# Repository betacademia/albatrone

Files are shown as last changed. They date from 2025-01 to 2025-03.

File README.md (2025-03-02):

# Albatrone

For the biomimicry minor of the Makerspace, localised at the University of Amsterdam, team Albatrone has done some design and research. The final part of the paper, documentation, will mostly refer to this repository, since it will contain all the (final) digital work done for the minor.

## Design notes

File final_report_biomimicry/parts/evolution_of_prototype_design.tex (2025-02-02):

\sectionauthor[Simon Blom; Romy Schardam]{Evolution of Prototype Design}
% This chapter is where you document the entire journey of your prototype's development. It should not only showcase your final product but also the thoughtful and iterative process that led to its creation. This narrative should be detailed and reflective, offering a comprehensive and transparent view of your design process. This chapter is your opportunity to demonstrate your team's problem-solving skills, adaptability, and ability to integrate feedback into a practical solution.
% \begin{itemize}
%     \item Step-by-Step Evolution: Describe each stage of your prototype's development. This should include the initial concept, any interim versions, and the final design. For each step, explain the rationale behind the design choices made, focusing on both the successes and challenges you encountered.
%     \item Design Motivation: Detail the motivations for each design change. These motivations can be varied - they might stem from your own insights, experimentation, feedback from stakeholders, or new information from scientific literature. It's important to articulate why each change was made and how it contributes to the overall effectiveness of your prototype.
%     \item Stakeholder Input: Discuss the stakeholders involved in your project, providing insights into their perspectives and how their feedback has influenced your approach. For each stakeholder, include a concise summary of the interview. These summaries should be approximately half a page each and should detail the stakeholder's role, their perspective on the problem you are addressing, and any specific insights or recommendations they provided. Clearly indicate which team member conducted each interview.
%     \item Influence of Stakeholder Insights: Specifically address how stakeholder input influenced your design evolution. Explain how their insights led to adjustments in your design, alterations in your theoretical approach, or shifts in your understanding of the societal impact of your solution. This aspect should clearly link the feedback you received to tangible changes in your prototype.
% \end{itemize}

\section{The beginning of the project} 
At first, the idea was to make a drone that could take other drones out of the air by flying into them. This idea was quickly shut down as it became clear that this would involve a lot of precision when calculating the flight trajectory of the other drone, making sure our drone was fast enough to catch up, and making sure it could change its trajectory really fast when needed.

The brainstorming continued and eventually led to the idea of the Albatrone. A fixed wing drone with the aim to increase the airtime of the drone which could be used for search and rescue applications.  

\subsection{Problem statement}
The aim of the Albatrone is to solve the problem of the limited airtime of drones. Drones like a quadcopter need constant energy to keep flying. This leads to the need for a large, and most likely heavy, power supply when the drone needs to be in the air for a longer amount of time. Thereby adding to the energy needed to keep the drone in the air. The goal is to make a drone that is able to take advantage of its environment. With the fixed-wing design, the Albatrone will be able to glide through the air, eliminating the need for a constant power supply. 

\subsection{Midterm proposal}
\subsubsection{Background information and research}

In the beginning, the choice was made to take inspiration from the albatross. This decision was made on the basis of a quick google search on the top birds that use gliding to save energy during long flights. Adding to the fact that the wandering albatross has the biggest wingspan out of all birds and that the albatross is a heavy bird, this decision was quickly accepted by all members of the team.  

To solidify this decision even further, research was done on the different properties, like the lift coefficient, drag coefficient, and the relation of both coefficients to the angle of attack, of a few foils (cross sections of the wing) that were based on different animals. For this XFoil was used. XFoil is a software developed at the Massachusetts Institute of Technology. XFoil is an interactive program for the design and analysis of subsonic isolated airfoils (\cite{XFoil}). Within the database, there are three different albatross foils
\begin{itemize}
    \item GOE 176 (ALBATROS 7020) AIRFOIL (goe176-il) (\cite{Foil_176}) - one dragonfly foil (\cite{Flcn})
    \item GOE 174 (ALBATROS 5020) AIRFOIL (goe174-il) (\cite{Foil_174}) - a falcon foil (\cite{Drfly})
    \item GOE 173 (ALBATROS 6020) AIRFOIL (goe173-il) (\cite{Foil_173}) - a wasp foil (\cite{Wasp})
\end{itemize}
and when comparing all these foils, the dragonfly foil came out on top.

Another conformation is found in the paper called ‘Aerodynamic characterization of an Albatross wing for Bio-inspired unmanned aerial vehicle’ (\cite{Bio_unmanned}). In this paper, the researchers found that the albatross wing has a higher lift coefficient, and a lower drag coefficient compared to the wing shapes of the other birds.

The way in which the albatross can traverse long distances without needing a break is also due to the way in which the albatross harnesses the energy from its environment.

One interesting aerodynamic interaction of the wings is created by the Bell-Shaped Lift Distribution (\cite{Evolution_Alba}).

Lift is generated by vortices. In the Bell-Shaped Lift Distribution, the vortices are shed at around 70-80\% of the span. This explains why the wingtips of the albatross are not going up even when they undergo speeds around 3G during dynamic soaring. The benefit of a Bell Shaped Lift Distribution is that it generates a local induced thrust. Although the net force still results in net drag, this local thrust is interesting (\cite{Evolution_Alba}). 

The albatross uses two types of soaring: dynamic soaring and thermal soaring.\\

In dynamic soaring, the albatross makes use of the varying wind speeds above the sea surface. Dynamic soaring consists of four stages, the climb into the wind (wind ward climb), the turn at high altitude, the leeward descent, and the low-altitude turn (see Figure \ref{fig:Dynamic soaring}). During this cycle, the albatross has a decrease in energy when it is close to the water, but an increase when it climbs the wind. Because the albatross gains its energy back, it takes almost no energy to keep it in the air (\cite{Evolution_Alba}). 

\begin{figure}
    \centering
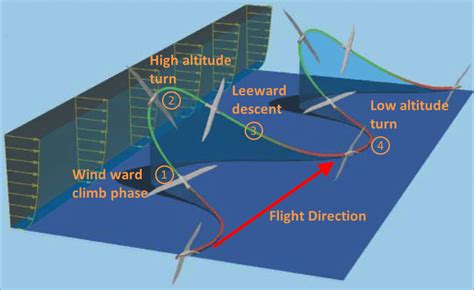
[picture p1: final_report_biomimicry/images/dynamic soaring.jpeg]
    
    \caption{Dynamic soaring cycle (\textit{https://www.researchgate.net/figure/Dynamic-soaring-cycle_fig1_326672558})}
    \label{fig:Dynamic soaring}
\end{figure}

Next is thermal soaring. During thermal soaring, the albatross flies through or circle in columns of warm air currents that rise from the ground. The rate of descending of the bird is less than the magnitude of the rising air. This makes it possible for the birds to attain more altitude, see Figure (\ref{fig: thermal soaring}). With this extra altitude, the albatross is able to glide to the next thermal (\cite{Evolution_Alba}). 

\begin{figure}
    \centering
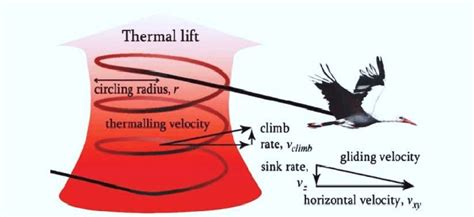
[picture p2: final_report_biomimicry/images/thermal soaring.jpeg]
    
    \caption{Thermal soaring (\textit{https://www.researchgate.net/figure/Thermal-Soaring-16_fig4_352395064})}
    \label{fig: thermal soaring}
\end{figure}\\

This paper also mentions that even the colors of the wings can have some effect on the endurance of the bird. The temperature difference between the upper (black) and the lower (white) surface of the wings, aids in drag reduction. Temperature plays a significant role in the reduction of induced and skin friction drag.\\

Researchers found that the black-white or black-black wings performed better than the white-black or white-white coloring (\cite{Evolution_Alba}).\\

\subsubsection{What does the Albatrone take from the albatross?} 

Mostly, the shape and the dimensions of the wings. To make the wing structurally sound, the bones in the albatross wing will be taken as inspiration. This is done by having 3D printed joints and the ‘bones’ make out of pieces of balsa wood. The idea is to follow the shape of the wing as best as possible, also making sure the cross section is the same. \\

If possible, the tail feathers of the albatross could also serve as an inspiration for the horizontal stabilizers. For this to work, the placement of the propeller needed to be taken into account.
As told by the expert stakeholder ir. Madeline Zhang, the placement of the propeller has an impact on the stability of the drone. She mentioned that placing the propeller on the back of the drone makes it more stable as it does not cause the airflow over the wings to become turbulent. Placing the propeller in front, means an added risk of the drone back-flipping on take-off. If the propeller is mounted at the back of the Albatrone, the stabilizers should not obstruct the propeller.
 
\begin{figure}
     \centering
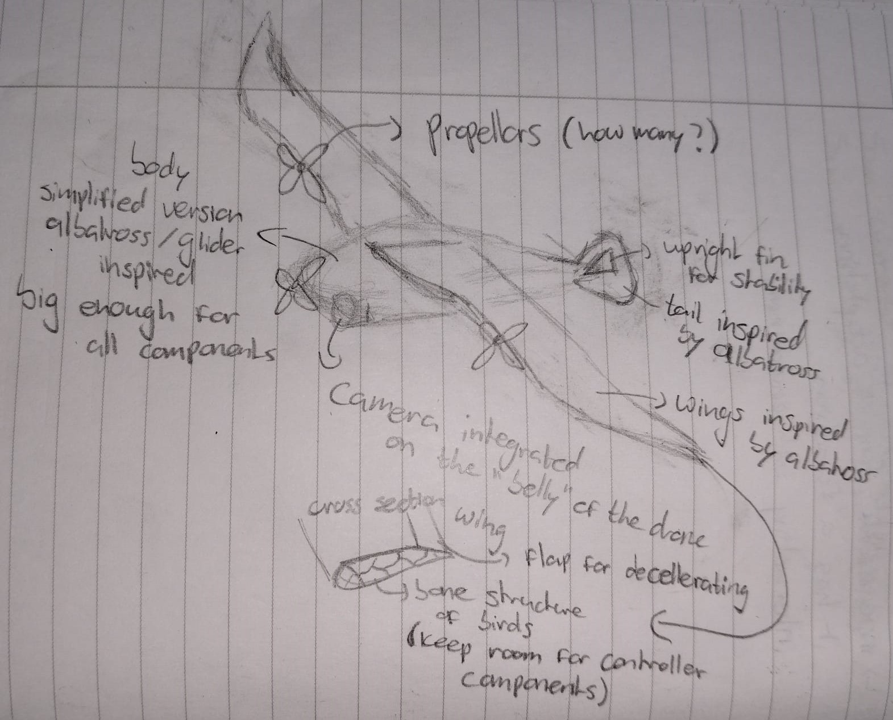
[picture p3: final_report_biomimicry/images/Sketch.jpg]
     
     \caption{One of the first sketches of the Albatrone}
     \label{fig:Sketch Albatrone}
 \end{figure}

 In figure \ref{fig:Sketch Albatrone}, one of the first sketches of the Albatrone can be seen. Highlighted are the wings, tail, body and bone structure that are inspired by the albatross. \\

\section{Design evolution} 

During the time between the project proposal and the final report, some changes occurred. 

\subsection{Material} 
In the beginning of this design process, our 'plan A' was to use a Carbonfiber-nylon filament (PAHT-CF). During a meeting with our expert stakeholder Ir. Madeline Zhang, she mentioned that making the Albatrone out of balsa wood and shrink foil would be a good option to keep it lightweight. While making the Albatrone out of wood was an option, the availability and prices online, plus the lack of modes of transportation to get the wood to the Makerspace, made this option not final. The people of the Technology Center also provided feedback during a project standup session. Here they mentioned that balsa wood and shrink foil might not be strong enough to hold the electronics. This lead to researching ways to improve the structural stability. I-beams were an option, but most I-beams are made of metals. A wooden I-beam was really expensive and not made of the lighter balsa wood.

Another option that was presented by the project staff was styrofoam. This option was briefly explored. However, the shaping needed to be done with a foam cutter. This required a steady hand from the cutter and the shape of both wings needed to be the same. Having two identical but mirrored versions of an albatross wing out of styrofoam, seemed unlikely.

With a little more research, a different filament, Bambu PLA Aero, was found to be suitable for the Albatrone. This filament is a sort of "active foaming PLA" specially advertised by use for Remote Controlled Planes (\cite{PLA_Aero}). This change did mean that some different dimensions were needed as every part needed to fit in the BambuLab X1 Carbon or X1E. This also meant that 3D printed 'joints' and wooden 'bones' were no longer needed. While losing this bio-mimicry component, it now became possible to incorporate the hollow bone structure of birds by the configurable sparse infill of those 3D printers. Again, the people from the Technology Center provided feedback. They were a little hesitant at first and mentioned that most plastics had a similar density and could be too heavy for our application. On the other hand, when the properties of the PLA Aero were explained, they became intrigued. This solidified our choice in material.

When ordering the filament, Murphy's law struck again. On the website of `Electronica voor jou', it said that there was one roll of black PLA Aero available. The filament was ordered on the 10th of December, after contacting the business three separate times and waiting for over a month (13th of January), they finally said they could not order this specific PLA. The PLA Aero was ordered by a different business, only this time in white. As mentioned in the 'Background information and research' part, black-white or black-black wings create (even if it is just a little) less drag compared to the white-black or white-white wings. While this color change will most likely not be responsible for big changes in the performance of the Albatrone, especially during winter, it could be interesting to try and recreate these findings on the Albatrone in the future. While waiting for the right filament to arrive, parts of the design was printed using regular PLA. These prints were used to test the way the parts are attached to each other and the tolerances of the BambuLab printers.

\subsection{Wing dimensions} 
Another change, the dimensions of the wings. The biggest chord length was estimated to be around 270 mm for the smaller gray-headed albatross. This was based on an estimation that the wing is roughly 1/3 of the length of the body of the albatross. This estimation came from measuring a picture of the gray-headed albatross from google. 

The length of the body of was found to be in the range of 71 to 82 cm (710 to 820 mm) (\cite{WoRMS}).

To get the top view of the wing, the length of the bones (humerus, ulna, and the manus + primaries) were used to get an idea of how long each part must be (\cite{Wing_shape}). The wingtip is put at a 60 degree angle to make it easier to calculate the area of the wing. 

In the same paper, the aspect ratio of the gray-headed albatross (or the Diomedea chrysostoma), is found to be 15.3. with a wingspan of 200 cm.  

To find the aspect ratio, the wingspan squared is divided by the wing area.\\

To get to an aspect ratio close to this 15.3, the chord length needed to be smaller than expected.\\

Calculating the aspect ratio should be somewhat simple. Unfortunately, it would not be a (school) project without even the smallest things going wrong. A while after using the aspect ratio as a guide on how big the chord length of the different parts of the wing should be and keeping in mind that during this calculation the dimensions of the body was just an estimate, the realization that in all those calculations the area of the body was wrongly calculated came a little too late.\\

As mentioned above, the chord length started at 270 mm. Limited by the dimensions of the 3D printer, this became 250 mm. After realizing the mistake in the calculation of the aspect ratio, the only 'quick fix' that came to mind was to make the first part of the wing shorter both in length and width as the thickness needed to intergrade the servo that controls the ailerons in the middle part of the wing, was set to 145 mm. The maximum chord length ended up being 150 mm which quickly goes to 145 mm for most of the wing.\\

\subsection{Body} 
The journey to the perfect body. In the beginning, the idea was to make the body a more simplified version of that of the albatross. This meant following the general shape of the albatross without the beak. However, designing organic shapes in SolidWorks or Fusion was proven to be tricky as is evident by the first attempt of the wing design in Figure \ref{fig:Fusion wing fail}.\\

\begin{figure}
    \centering
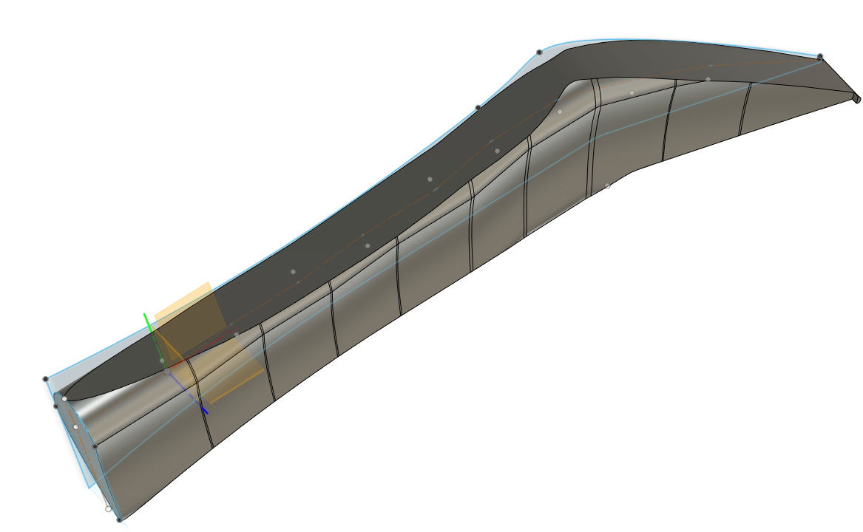
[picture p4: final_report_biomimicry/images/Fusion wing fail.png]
    
    \caption{First attempt designing the wing in Fusion}
    \label{fig:Fusion wing fail}
\end{figure}\\

To keep the design manageable, the body ended up more cylindrical as can be seen in Figure \ref{fig:Cylindrical body}, but not without trying the other things that came to mind.\\

The first few iterations mostly resembled a bullet shell, see Figure \ref{fig:bullet shell} and \ref{fig:Unfinished bullet}. In the second figure, the idea was to make the walls straight to make it easier for the wings to attach to the body. Figure \ref{fig:Eehm...no} was an attempt to make a symmetrical body with straight walls for the wing attachment. This did not really work. So, a little more thinking was needed before going to SolidWorks.
The resemblance to a bullet occurred most likely because the head and body were attached together. Again, because the limitations of the available printing dimensions, this was not the right approach. \\

To get the desired length of the whole body, the body, head and tail were separated. To make sure the inside of the body could be reached, a part of the body was cut horizontally. Next slots were added to be able to attach the rest of the body to this open part. The head, tail and wings would hopefully keep the body closed during flight. Figure \ref{fig:Cylindrical body} and \ref{fig:Oval top} were designed more carefully.

\begin{figure}
    \centering
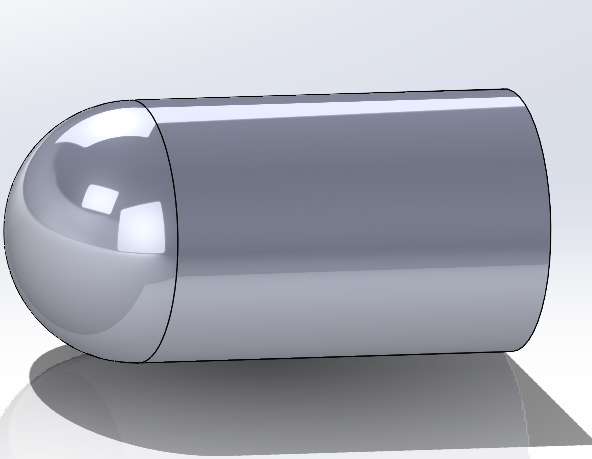
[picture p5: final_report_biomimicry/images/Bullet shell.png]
    
    \caption{Bullet shell body}
    \label{fig:bullet shell}
\end{figure}

\begin{figure}
    \centering
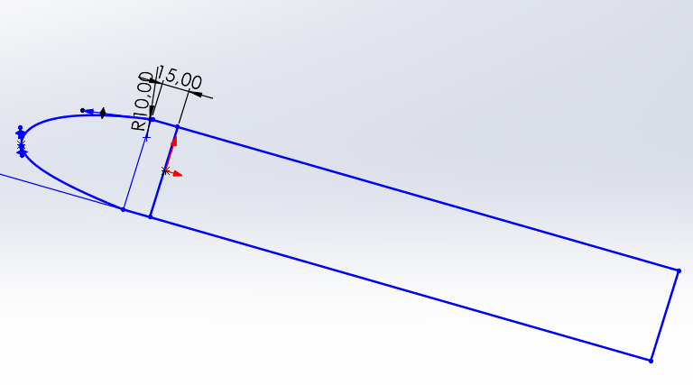
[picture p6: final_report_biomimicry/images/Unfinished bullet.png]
    
    \caption{Sketch straight-walled bullet body}
    \label{fig:Unfinished bullet}
\end{figure}

\begin{figure}
    \centering
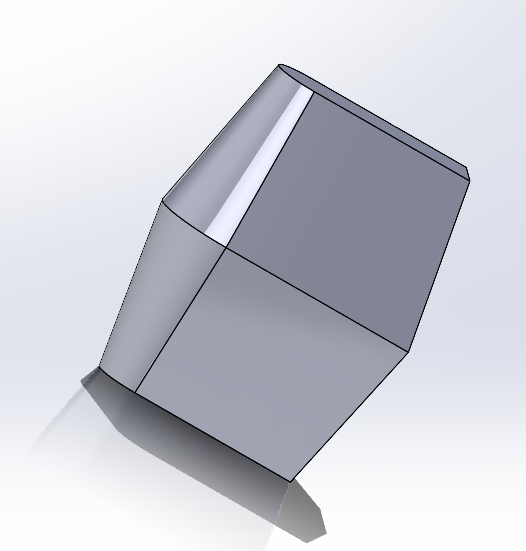
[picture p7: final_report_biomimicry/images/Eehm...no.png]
    
    \caption{Attempt to make a symmetric, straight-walled body}
    \label{fig:Eehm...no}
\end{figure}

\begin{figure}
    \centering
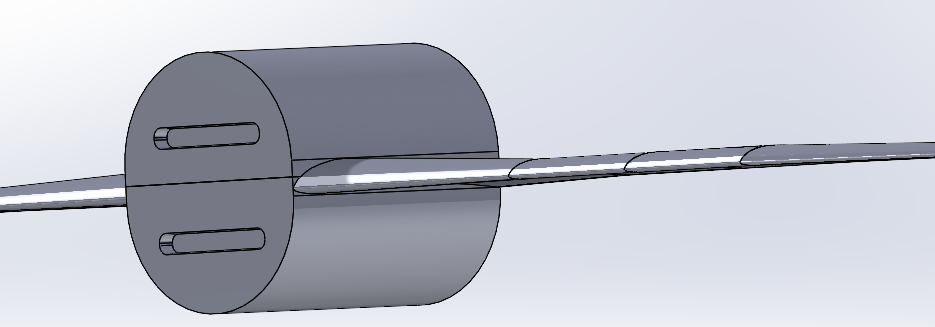
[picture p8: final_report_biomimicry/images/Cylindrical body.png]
    
    \caption{Cylindrical body}
    \label{fig:Cylindrical body}
\end{figure}

\begin{figure}
    \centering
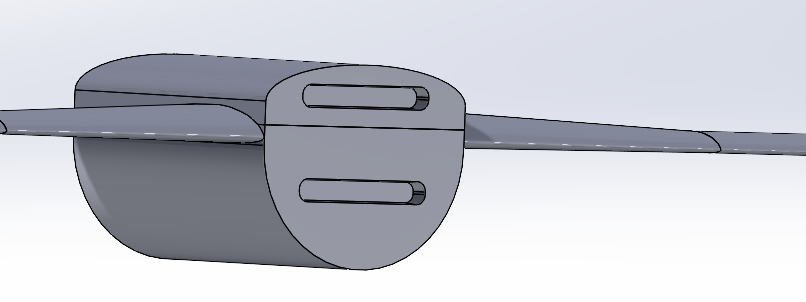
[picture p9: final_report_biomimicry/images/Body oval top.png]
    
    \caption{Body with oval top}
    \label{fig:Oval top}
\end{figure}

Not only the shape of the body went through some iterations, but also the dimensions. The planned width of the body was around 200 mm to get the wingspan close to the 2 meters from the gray-headed albatross. In the end, this changed. The choice was made to design the body as small as possible, while still being able to hold all the electronics. This decision was based on the insight that the body would most likely only negatively affect the aerodynamics as the bulk of the body would be a cylinder. The design in Figure \ref{fig:Cylindrical body} was first made with a radius of 55 mm on the outside with a wall thickness of 2 mm. This made the whole body quite big in relation to the cross-section of the wings. To save on material, weight and hopefully improve on the aerodynamics, the top was designed to be more oval. This change did not go as smoothly as thought. SolidWorks began moving points when changing the height of the ellipse in the sketch or did not connect the sketch of the ellipse to the right point in the sketch. This made it quite difficult to accurately design the body. After deleting, redrawing, and double checking the sketches again and again, the body did eventually line up. However, in the mean time, the electronic parts had arrived. This meant that is was now possible to design the body more around the electronics. This took away the some of the guesswork with regards to the size needed. With a smaller body, the drag would decrease and the weight would decrease, resulting in better aerodynamic properties. Keeping the issues with the oval top in mind, this smaller body design went back to the two half circles as seen in Figure \ref{fig:Cylindrical body}.

\subsection{Tail} 
The main goal for the tail is to be able to stabilize the drone with the vertical and horizontal stabilizers [https://aerotoolbox.com/design-aircraft-tail/]. The process of designing the stabilizers is explained later. For the shape of the tail of the Albatrone, inspiration was taken from pictures of the tail of planes. Looking at pictures of planes, it was noted that in a lot of pictures, the underside of the tail curves up. Keeping the top line of the plane straight. Figure \ref{fig:Tail v1} shows the first iteration of the tail. Figure \ref{fig:Albatrone small body} shows the tail more in line with the top of the body.\\

\begin{figure}
    \centering
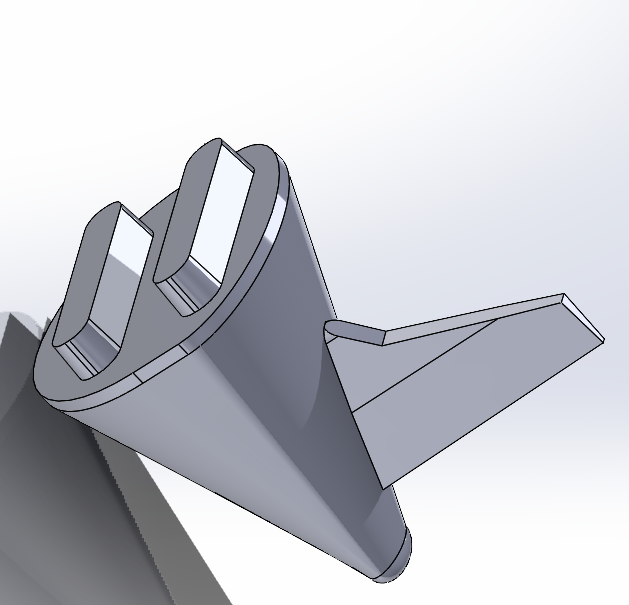
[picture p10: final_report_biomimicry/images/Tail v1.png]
    
    \caption{Tail design more centered on the body}
    \label{fig:Tail v1}
\end{figure}

\begin{figure}
    \centering
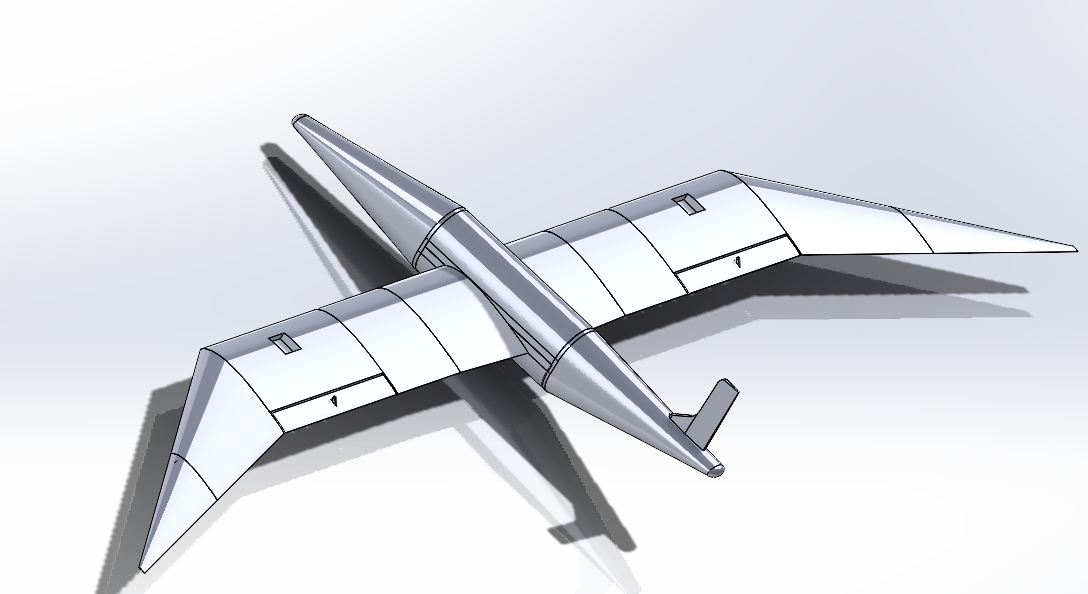
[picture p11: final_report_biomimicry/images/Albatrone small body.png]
    
    \caption{Albatrone where tail is more in line with the top of the body}
    \label{fig:Albatrone small body}
\end{figure}

\subsection{Head} 
As mentioned before, first the design for the head mostly resembled a bullet shell. When it became clear the body also needed to be printed in sections, the head of the Albatrone became more of a cone shape, similar to the tail, as can be seen in Figure \ref{fig:Albatrone small body}. However, this was mostly due to a lack of knowledge on how to create a more plane-like nosecone, With the help from a YouTube tutorial called 'Solidworks Loft Basics - Design an Aircraft Nosecone (CAD Tutorial for Beginners! - B737 \& F-22)' from VDEngineering, the nosecone became more similar to a 'normal' nosecone from a plane (\cite{Nosecone}). To follow this tutorial, a side, top, and front view was needed. This, unfortunately, meant that it was not possible to just use any picture. To still keep the spirit of using the albatross, a blueprint of the Aero L-39 Albatros was used to design the head (\cite{DrawingNC}). With the help of the tutorial, the head now looked as in Figure \ref{fig:Plane nose}. The choice of the plane was purely based on the name and which plane seemed to have a pointier nose as to mimic the beak of the albatross even if it is just a little. If time had allowed, it would be possible to create multiple noses and see which one worked better. Unfortunately, this was not possible in the time that was left for the project.\\

\begin{figure}
    \centering
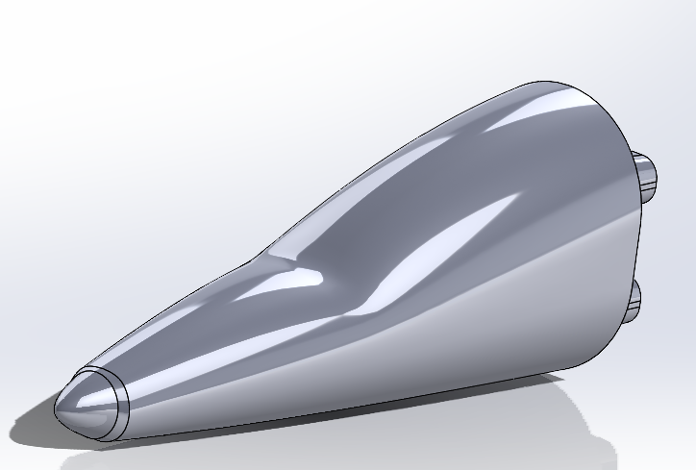
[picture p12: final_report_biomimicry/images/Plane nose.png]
    
    \caption{Head inspired by the Aero L-39 Albatros}
    \label{fig:Plane nose}
\end{figure}
\\

\subsection{Control surfaces}
To be able to control the drone, control surfaces are needed. An overview of the control surfaces of a plane can be seen in Figure \ref{Control surfaces} For the wings this meant that one middle part needed a flap to be able to manipulate the airflow around the wing (ailerons). At first, to test if it was possible, a small rectangular grove was cut out of the wing. This resulted in a totally detached flap that needed to be accurately positioned on both sides of the wing to keep symmetry. Next, the idea was to keep the upper part of the flap attached to the wing and making the cut on the bottom at an angle to make it able to go down. This would fix the problem of the positioning but decreases the mobility. Also, this idea would take some trial and error as the thickness of the connection would determine the force needed to move the flap. The higher the force needed to move the flap, the more powerful (and most likely bigger and heaver) the servo needs to be.\\

\begin{figure}
    \centering
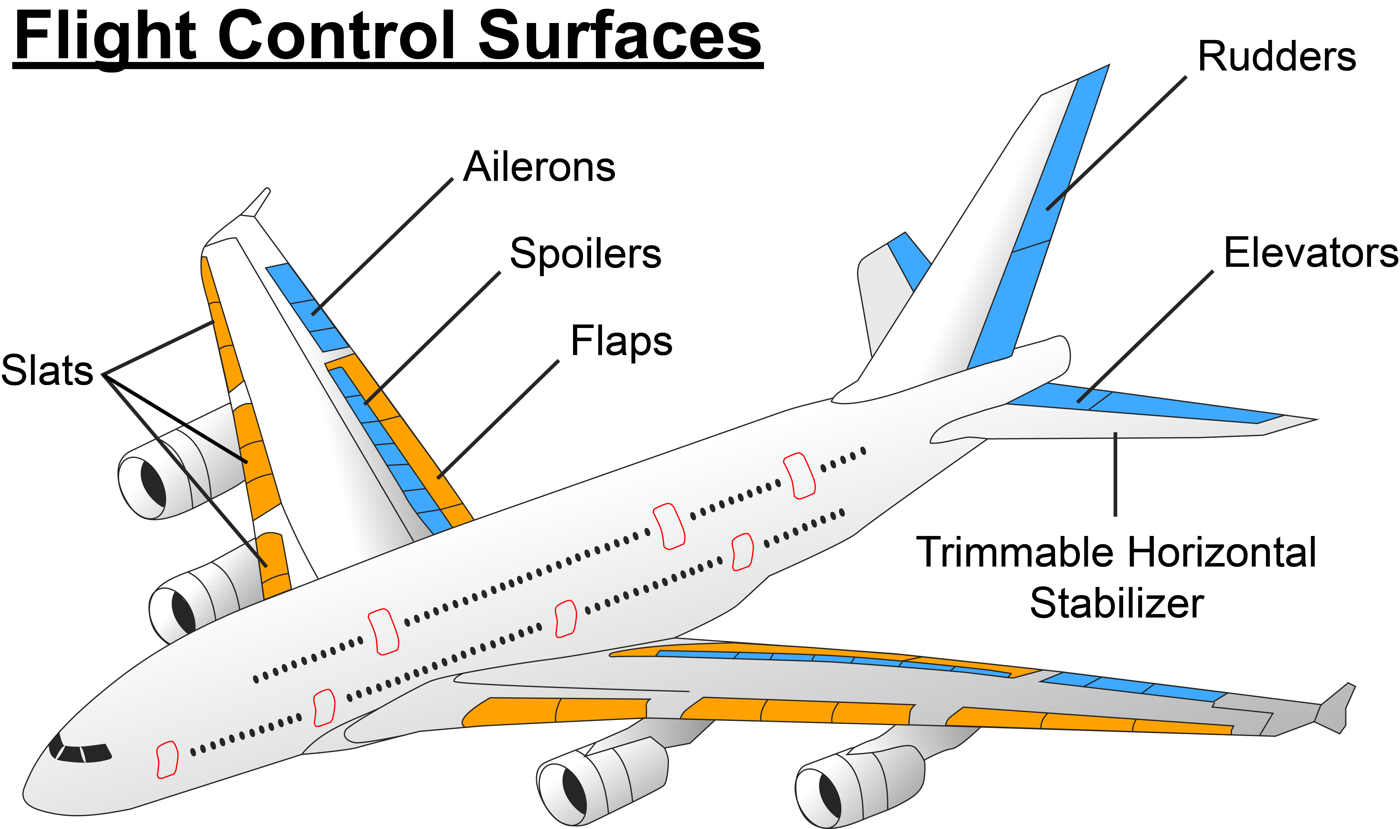
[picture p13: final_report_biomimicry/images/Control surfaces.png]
    
    \caption{Overview of the control surfaces of a plane (\textit{https://www.naii.com/DesignExamples/TestingAircraftControlSurfaces})}
    \label{Control surfaces}
\end{figure}

Eventually, the design is based on a tutorial found on youtube.com called 'Solidworks | Wing control surface animation | Aileron animation in solidworks' by Rao Aerospace (\cite{Aileron}). In this design the aileron is attached to the rest of the wing with a rod. For the Albatrone, a longer skewer should do the trick.

As for the vertical stabilizer, the first attempt was just a rectangle on the tail. After taking some inspiration from google images on tails of planes, there was an attempt to make it a little more aerodynamic. This resulted in the design in Figure \ref{fig:Sketchy vertical stab}.

\begin{figure}
    \centering
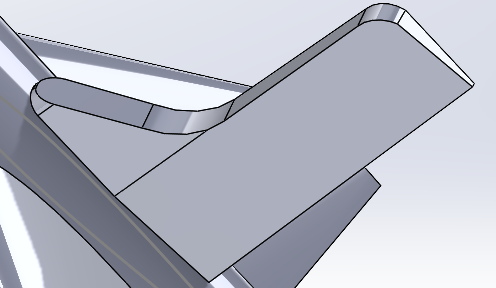
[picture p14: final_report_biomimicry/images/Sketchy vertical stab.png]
    
    \caption{Attempt at making the vertical stabilizer more aerodynamic}
    \label{fig:Sketchy vertical stab}
\end{figure}

Realizing the horizontal stabilizers are quite important as they make sure a plane is stable during a flight, more research needed to be done. First, another expert stakeholder, a neighbor of one of the members of the team (Romy) and an retired pilot that sails as a hobby, was nice enough to lend out his study books on planes, high-speed aerodynamics, and even one on the aero-hydrodynamics of sailing. While being very interesting, these books talked more about how to control a plane and not really on the design of the plane. However, during the talk with the neighbor, he advised to use the a wind tunnel to figure out what design works better and could be implemented in the design. He mentioned that calculations are nice, but some things cannot be calculated. Therefor, having access to a wind tunnel and analyzing the results, was more useful. Again, if time had allowed, adding different stabilizers to the Albatrone and noting the difference in the stability, would be ideal.

Focusing on the design of the stabilizers, a google search lead to a more useful page on Aircraft Horizontal and Vertical Tail Design (\cite{Stablizers}). This page mentions the different configurations, a relation to calculate the minimum area of the stabilizers based on some parameters from both the wing and the horizontal stabilizer itself. This page also presented an answer on the question what shape could be used for the stabilizers. A very common choice is apparently either the NACA 0010 or NACA 0012 airfoil. Comparing these airfoils again on airfoiltools.com, the NACA 0012 looks to be a little more stable than the NACA 0010, thus the decision on the airfoil for the horizontal stabilizers was made. Figure \ref{fig:Horizontal stab} shows the end result of hours full of struggling with lofts, deleting and redrawing the sketch of the curves on the sketch plane, and checking again and again if the two stabilizers are in fact symmetric and placed at the same location on the tail. At the time of writing, the elevators and the corresponding servo attachment and designated servo spot are not yet implemented.

Because this airfoil is most likely more aerodynamic than the vertical stabilizer seen in Figure \ref{fig:Sketchy vertical stab}, this airfoil will also be used as the vertical stabilizer (not yet implemented at time of writing).

\begin{figure}
    \centering
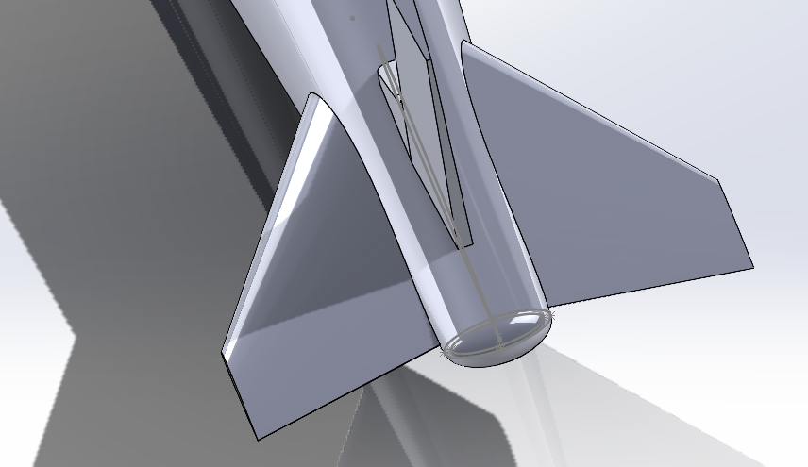
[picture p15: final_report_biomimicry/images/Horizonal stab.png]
    
    \caption{Horizontal stabilizers}
    \label{fig:Horizontal stab}
\end{figure}\\

\subsection{Connections}
It should not come as a surprise that the Albatross is made of separate parts. All those separate parts need to be connected. The connection between the different parts of the wing was quickly designed.The people of the Technology Center were not entirely sure these connections would hold up because of the stress concentrations created by such a connection. However, when testing the connections when printed with regular PLA, they proven to be strong enough to withstand the not-so-scientific stress test called 'trying our best to break them using our hands'. Another option, more in the direction of duck tails, see Figure \ref{fig:T-ducktails} was also tested. The test print looked as in Figure \ref{fig:Attachment test}. As the tolerance on these test prints was too large for our application, this idea was scrapped. 

\begin{figure}
    \centering
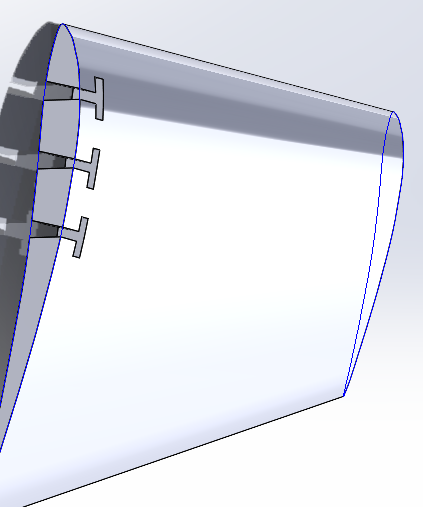
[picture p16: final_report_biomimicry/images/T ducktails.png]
    
    \caption{T-shaped duck tail inspired attachment method}
    \label{fig:T-ducktails}
\end{figure}\\

\begin{figure}
    \centering
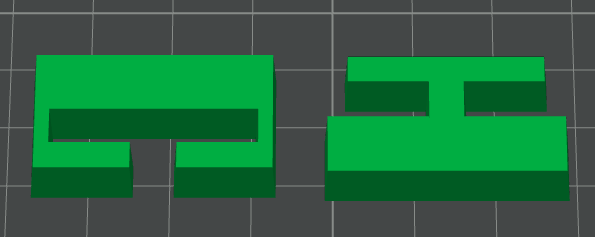
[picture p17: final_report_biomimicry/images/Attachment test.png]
    
    \caption{Test print T-shaped ducktails}
    \label{fig:Attachment test}
\end{figure}

The connection between the wing and the body required a little more thought. To test the best angle of attack for the Albatrone's wings, this attachment needed to allow one degree of freedom, the rotation. To allow for this rotation, a pin and hole connection was implemented; see Figure \ref{fig:Body pin connection}. Also visible in this figure are the connections between the other parts of the body (see \ref{fig:Tail v1} for the other part of the connection)

\begin{figure}
    \centering
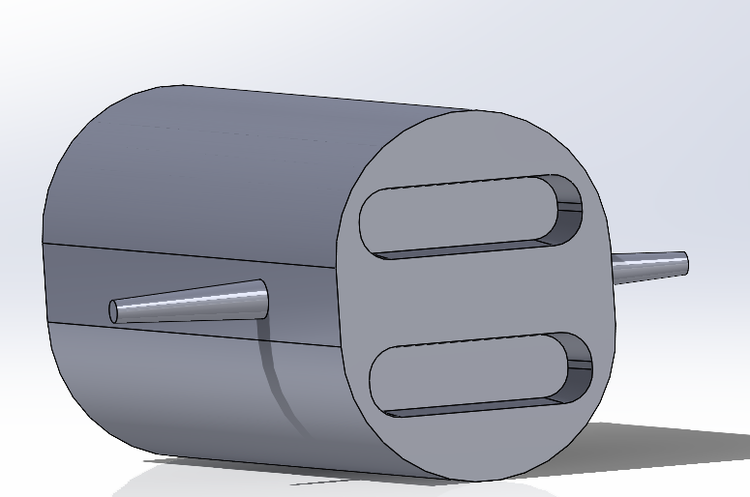
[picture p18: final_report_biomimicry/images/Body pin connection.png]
    
    \caption{Body with pin to connect to the wing}
    \label{fig:Body pin connection}
\end{figure}

As described above, this middle part of the body is cut in two to make it easy accessible. These two parts are held together by the pin-hole connections between the body and the wing and also by the extrusion and hole slots in the extra body parts made in order to get the desired length.\\

\subsubsection{Final design}
After implementing aforementioned design choices, the current final design can be seen in Figure \ref{fig:Final design}. The horizontal and vertical stabilizers are not finished yet. The horizontal stabilizers need elevators and room for the servo. The vertical stabilizer will be changed to the NACA 0012 airfoil. At the time of writing, the printing of the Albatrone is not done and is therefor also not tested. If in the next few days changes need to be made, this will obviously not be recorded in this specific report.

\begin{figure}
    \centering
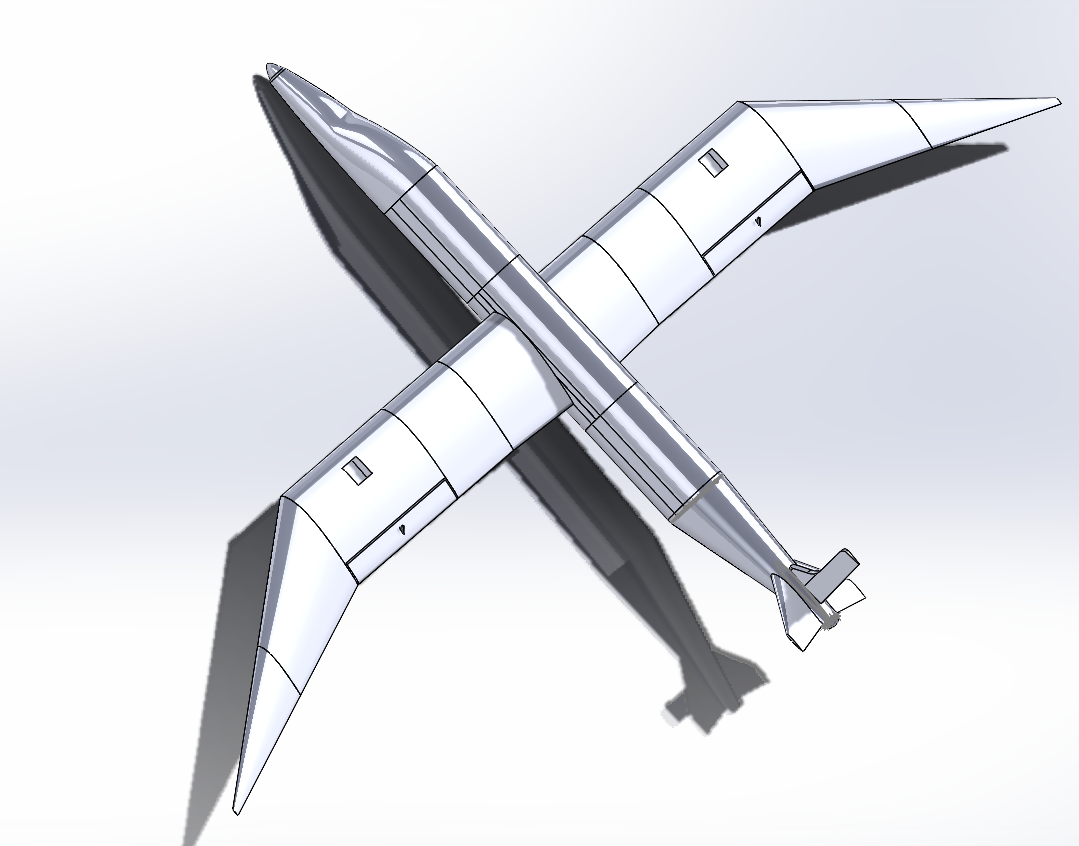
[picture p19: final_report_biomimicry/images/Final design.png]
    
    \caption{Final design}
    \label{fig:Final design}
\end{figure}

\subsection{Stakeholders}
As briefly touched upon in the text above, some design changes were made due to feedback or insights from stakeholders.

In the morning of November the 4th, we had a meeting with a police detective and specialist on the drones unit. Before the meeting, the idea was to use a combination of Lidar and Radar to obtain information about the surrounding. He explained to us that a simple camera can be enough. The power of machine learning is so powerful, that the algorithm can help more than enough. He also redirected us to an initiative called Avy. Avy makes the drone and finishes the paper work, so that the police can buy it and use it immediately. Avy was not responsive for a long period of time, but it was managed to make an appointment in the week of the presentations.

In the afternoon of November 18th, one of the members of the team attended the opening of E.N.G.A.G.E. which is the first so-called gameroom in the Department of Defense. It was organized by the "Korps Mariniers", and there were a lot of demos at the location. One of those demos was about Unmanned Aerial Systems (UAS), by the Head Coordinator of the Marine training center. I told him about our project, and we exchanged contact information. Around 10 days later we got an email cc'd from him, asking a colleague if he knew someone to help us out. 10 more days later, he responded and we were referred to someone else. This started a chain of replies and forwards, and January 20th we ended up with a specialist from the UAS programme inside the department of Innovation. Unfortunately we haven't had any response as of writing this report.

In the evening of 3 January 2025, a neighbor of one of the members was available for a talk about the Albatrone. This neighbor is a retired pilot and sails as a hobby. As this was during the Christmas break, she went alone. During this talk, the SolidWorks parts, that were finished at the time, were presented. As this neighbor has a lot of knowledge regarding the handeling of and the aerodynamics around a plane, some different design choices made in different planes, specifically KLM (Koninklijke Luchtvaart Maatschappij voor Nederland en Koloniën N.V.) planes and their impact on the aerodynamics were discussed. After this nice talk, the neighbor was kind enough to lend out some older books about piloting and what happens around an aircraft during flight. Also another book about the aero-hydrodynamics was also handed out, just in case.

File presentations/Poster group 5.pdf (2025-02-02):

What (the idea):
The goal of the Albatrone is to be able to travel long distances with a minimal amount of energy consumption by gliding through the air instead of flying when possible. The Albatrone will be build out of cheap materials so we can reach a wide range of customers, including the ones who have a little less to spend!

How (biomimicry)?
Inspired by the wings of the albatross, the Albatrone will have a wide wingspan to glide through the sky for long distances, making it more energy efficient as the use of a constant propulsion method is eliminated.

For whom?
The aim is to make the Albatrone as cheap as possible to ensure everyone who needs it, will be able to purchase it. The Albatrone is suitable for operations like: search and rescue operations, surveillance, and monitoring.

Why?
Centuries ago, people became fascinated with the idea of flight. Off course, this led to the planes and drones we have today. The main question to ask was ‘What if we took inspiration form nature to improve on those designs, will that make a difference?’

Technical components:
To control the Albatrone, propellors are needed, especially for when the conditions are not optimal. With the integrated camera, it will be possible to capture footage to help identifying people or other objects on the ground.

## The Abatrone

When drone meets nature
Group 5: Simon Blom, Sameh Mikhail, Romy Schardam

UvA minor Biomimicry
project 2024/2025

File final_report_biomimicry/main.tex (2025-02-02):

%-------------------------------------------------------------------------------
% LATEX TEMPLATE ARTIKEL
%-------------------------------------------------------------------------------
% Dit template is voor gebruik door studenten van de de bacheloropleiding 
% Informatica van de Universiteit van Amsterdam.
% Voor informatie over schrijfvaardigheden, zie 
%                               https://practicumav.nl/schrijven/index.html
%
%-------------------------------------------------------------------------------
%	PACKAGES EN DOCUMENT CONFIGURATIE
%-------------------------------------------------------------------------------

\documentclass{uva-inf-article}
\usepackage[english]{babel}

\usepackage[style=apa]{biblatex}
\addbibresource{references.bib}

%-------------------------------------------------------------------------------
%	GEGEVENS VOOR IN DE TITEL, HEADER EN FOOTER
%-------------------------------------------------------------------------------

% Geef je artikel een logische titel die de inhoud dekt.
\title{The Albatross: A Biomimetic Drone for Enhanced Search and Rescue Missions}

% Vul de naam van de opdracht in zoals gegeven door de docent en het type 
% opdracht, bijvoorbeeld 'technisch rapport' of 'essay'.
\assignment{Final report}
\assignmenttype{}

% Vul de volledige namen van alle auteurs in en de corresponderende UvAnetID's.
\authors{Simon Blom; Sameh Mikhail; Romy Schardam}
\uvanetids{14630591; 14003597; 15907635}
\studies{Artificial Intelligence; Physics and Astronomy; Mechanical Engineering}

% Vul de naam van je tutor, begeleider (mentor), of docent / vakcoördinator in.
% Vermeld in ieder geval de naam van diegene die het artikel nakijkt!
\tutor{}
\mentor{Mike Meulendijks}
\docent{Pim Linnebank; Morten Strømme; Mimi den Uijl}

% Vul hier de naam van je tutorgroep, werkgroep, of practicumgroep in.
\group{5}

% Vul de naam van de cursus in en de cursuscode, te vinden op o.a. DataNose.
\course{Minor Science, Technology \& Innovation: Biomimicry}
\courseid{5142DPB30Y}

% Dit is de datum die op het document komt te staan. Standaard is dat vandaag.
\date{\today}

%-------------------------------------------------------------------------------
%	VOORPAGINA 
%-------------------------------------------------------------------------------

\begin{document}
\maketitle
\begin{figure}[h]
    \centering
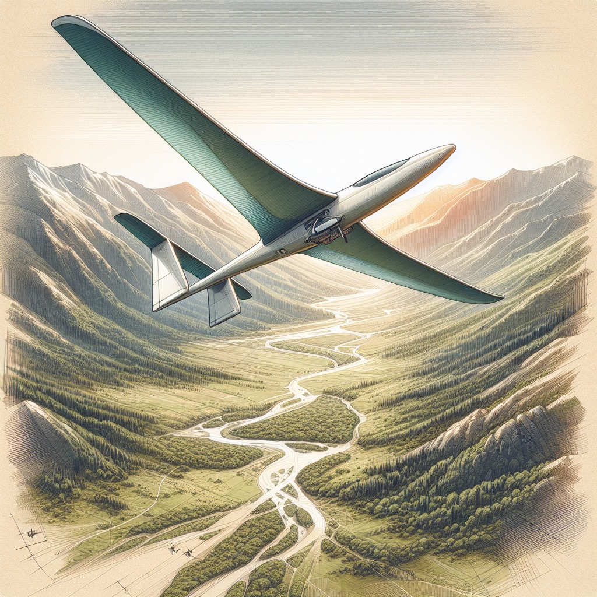
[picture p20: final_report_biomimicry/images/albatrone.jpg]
    
    % \caption{Caption}
    % \label{fig:enter-label}
\end{figure}
\newpage

%-------------------------------------------------------------------------------
%	INHOUDSOPGAVE EN ABSTRACT
%-------------------------------------------------------------------------------
% Niet toevoegen bij een kort artikel, zeg minder dan 10 pagina's!

%TC:ignore
\tableofcontents
%TC:endignore

%-------------------------------------------------------------------------------
%	INHOUD
%-------------------------------------------------------------------------------
% Hanteer bij benadering IMRAD: Introduction, Method, Results, Discussion.

\include{parts/abstract}

\include{parts/introduction}

% \include{parts/theoretical_framework}

\include{parts/evolution_of_prototype_design}

\include{parts/testing}

\include{parts/conclusion_and_discussion}

%-------------------------------------------------------------------------------
%	REFERENTIES
%-------------------------------------------------------------------------------

\printbibliography

%-------------------------------------------------------------------------------
%	BIJLAGEN 
%-------------------------------------------------------------------------------

%TC:ignore
\appendix 
\include{parts/documentation}
%TC:endignore

%-------------------------------------------------------------------------------
\end{document}

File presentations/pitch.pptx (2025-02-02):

## The Albatrone

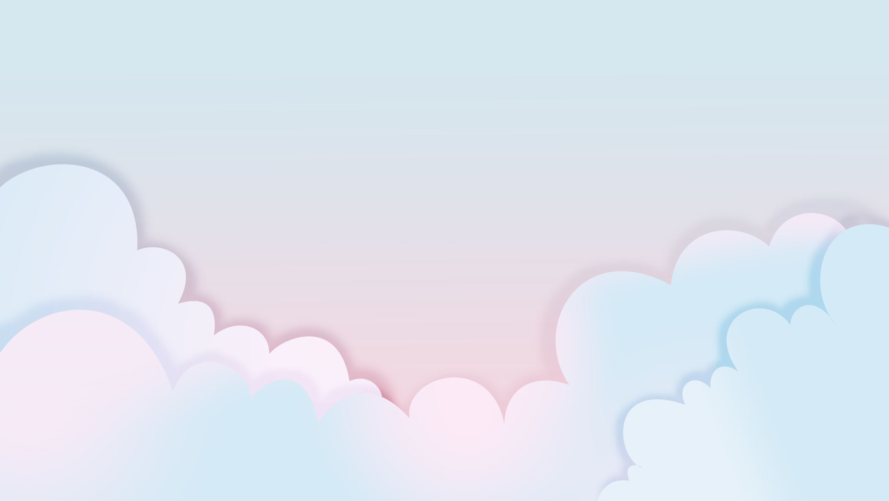
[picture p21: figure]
Roze en blauwe wolken

Simon Blom, Sameh Mikhail, Romy Schardam

## Introduction

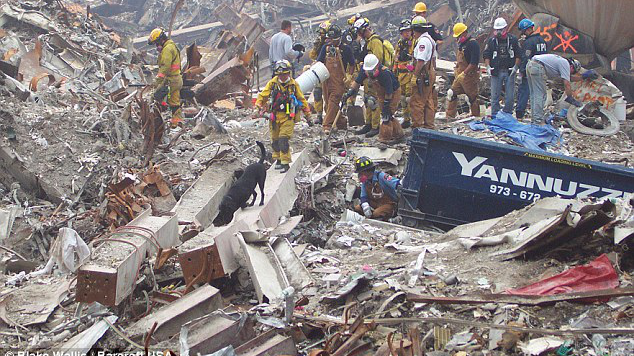
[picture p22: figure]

- Search and Rescue mission
  - Dogs
  - Police
  - Search parties
- Natural disasters?
- Minor missions?

Deze foto (https://jornalanimais.blogspot.com/2011/09/os-caes-do-11-de-setembro.html) van Onbekende auteur is gelicentieerd onder CC BY-NC-ND (https://creativecommons.org/licenses/by-nc-nd/3.0/)

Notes: Relevance and impact

## Bio-Inspiration

- Romy

## Technical Details

- Simon

## Future improvements

- Bigger

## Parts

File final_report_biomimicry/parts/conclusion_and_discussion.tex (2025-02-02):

\sectionauthor[Romy Schardam]{Conclusion}
Unfortunately, at the time of writing, the prototype is still under construction. A few parts are not finished yet, but it is expected that these changes can be implemented before the end of this project. \\

The journey to get to a flying robot/drone was not one without some setbacks. Between the long ordering times, faulty calculations and SolidWorks and the simulation software not working as expected, the time just seemed to go by too fast. However, the design of the Albatrone was made as best as the team could do under the circumstances.\\

The key aspect of building a bio-mimetic robot, is of course the relation to nature. In our design, this is done by taking inspiration from the albatross. The wing foil, wing shape and wing dimensions were designed to be as close to the actual albatross wings as possible. However, not all dimensions were available online. As a result, the wings are most likely not entirely accurate to the wings of an albatross. Another detail this drone takes from nature is the idea of hollow bones. Birds have hollow bones to make their bones lighter. The parts of the Albatrone are 3D printed and have a infill pattern to be more lightweight. Another possibility was to also take inspiration from the body of the albatross, but unfortunately, this was not in our skillset.\\ 

Of course, not every design choice was based on something in nature. Next to the albatross, inspiration was taken from drones, RC, and commercial planes. These influences can be seen in the body of the drone and in the electronic components. This was done to ensure the Albatrone would be able to be controlled during flight.

In the future, the Albatrone would have an integrated camera to actually be able to help on search and rescue missions as was the goal set in the beginning of this project. On the more ethical side, an integrated camera would put peoples privacy on the line when the drone is misused. To make sure the Albatrone is used for its designed purpose, the Albatrone would not be made available to the general public. Also, to make flying the Albatrone legal, buyers would need to have the right certification. This does create an initial barrier and requires some level of government influence.\\

Depending on if the Albatrone ends up being able to fly, in the future, it might be interesting to look into other materials that can be used to make this drone more lightweight. Also, as mentioned before, changing parts of the design and testing the effect of these changes on the aerodynamic properties using a wind tunnel, would help optimizing the design even more. 

\sectionauthor[Romy Schardam]{Discussion}
The Albatrone team started out as a group of four, but unfortunately ended as a group of three. This increased the workload on the remaining members. Adding the complexity of making a flying robot, this project did not go by without a few doubts in between. However, during this project, different skills were needed. No one from the team had build or designed a flying robot before. This created an initial set-back as first the knowledge needed to build something that could fly needed to be attained. In the end, it is still not sure if the final design works, but having to do the research, it takes a lot to be able to make something fly. The time available for this project, also limited the time that could be spend on acquiring this knowledge. But, some new skills were gained during this project, so even if the prototype is not ready, the experience stays.

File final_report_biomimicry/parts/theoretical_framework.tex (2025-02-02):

\sectionauthor[Simon Blom; Romy Schardam]{Theoretical Framework}
In the theoretical framework, the relevant literature for your project is introduced. This includes not only the literature that is incorporated into the project but also research that was considered but ultimately excluded due to feasibility. The theoretical framework forms the basis for the discussion, helping to contextualize the obtained results. It should include a consideration of the different sources and a justification for why certain literature was included or excluded from the project.

\begin{itemize}
    \item Theoretical Framework: Explores the scientific theories and biological phenomena that form the basis of your design. This section should demonstrate a robust understanding of the biomimicry component and its practical application in your project, supported by relevant scientific literature. It should also include scientific literature to support the non-biological (technical) aspects of your design.
    \item Deliberation of sources: The literature used in your theoretical framework should be evaluated, ultimately leading to a conclusion on which sources to include and which to discard. Describe how and why you adapted these concepts to achieve your prototype's objectives. This provides the foundation for your discussion later in the report.
    \item Relevance of the literature: The literature included in the theoretical framework should have a clear connection to the project. Use sources that are relevant, relatively recent, and appropriate for the project’s scope and context.
    \item Clarity and Structure: The theoretical framework should be logically organized. There are several ways to structure it, but choose a logical approach and maintain consistency.
\end{itemize}

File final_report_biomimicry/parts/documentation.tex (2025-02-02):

\sectionauthor[Sameh Mikhail]{Documentation}
Since the computer was used in this project, files and calculations were made and this project has a digital side. In the \href{https://github.com/betacademia/albatross}{Github repository}, everything used to create this project is stored. From the file used to do the data analysis to the design, the repo contains everything.

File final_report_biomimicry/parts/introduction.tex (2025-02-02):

\sectionauthor[Sameh Mikhail]{Introduction}
The official statistics of the United Kingdom's government show that the mean number of missing people in 2022/2023 is around 210 people per month (\cite{uk_search_and_rescue_2023}). In a time and world where mankind has put foot on the moon and where we can travel to the other side of the world, there are people missing in a medium-sized country. Even worse, the United Kingdom is no exception: When searching ``search and rescue missions'' on Google News, the most recent results are a few days and not limiting to a location. 

When people go missing, a search and rescue mission is initiated, involving various entities such as the police, rescue dogs, and volunteers (\cite{ncmec_search_and_rescue}), (\cite{us_doj_search_and_rescue}). However, traditional methods often have limitations, especially when it comes to covering large areas or difficult terrains (\cite{sar_review_2020}). This is where the Albatrone steps in, offering a innovative solution.

The Albatrone is a biomimetic drone modeled after the albatross, which is renowned for its ability to glide effortlessly over vast distances with minimal energy expenditure. Another interesting aspect of the albatross is the fact that it is a heavy bird, but it can still fly. The Albatrone is engineered to remain airborne for extended periods of time, making it a valuable asset to have during search and rescue missions. The key points of the Albatross are
\begin{itemize}
    \item energy efficient, so that it stays for a long period in the air
    \item easy user interface, so that the user does not need to have an intensive training to use it
    \item cheap, so that not only the police, but also non-governmental organisation and smaller organisations can afford it
\end{itemize}
and these should make an impact on search and rescue missions.

\subsection{Abstract}
The Albatrone, a biomimetic drone inspired by the albatross, offers an innovative solution to the challenges of search and rescue missions. The albatross's unique ability to glide long distances with minimal energy consumption serves as the foundation for this drone's design. By mimicking the bird's wing structure, aerodynamics, and energy-efficient flight techniques, the Albatrone is engineered to remain airborne for extended periods. Key features include a lightweight structure with 3D-printed hollow components, inspired by bird bones, and an intuitive user interface to ensure accessibility. Extensive testing, including wind tunnel experiments and material trials, informed the iterative design process, which integrates both biological insights and advanced aeronautical principles. Although the prototype is not fully constructed, the Albatrone demonstrates significant potential to enhance search and rescue capabilities, particularly in large or challenging terrains. Future developments could optimize its design, incorporate integrated cameras, and address ethical concerns regarding privacy to fulfill its mission-driven purpose.

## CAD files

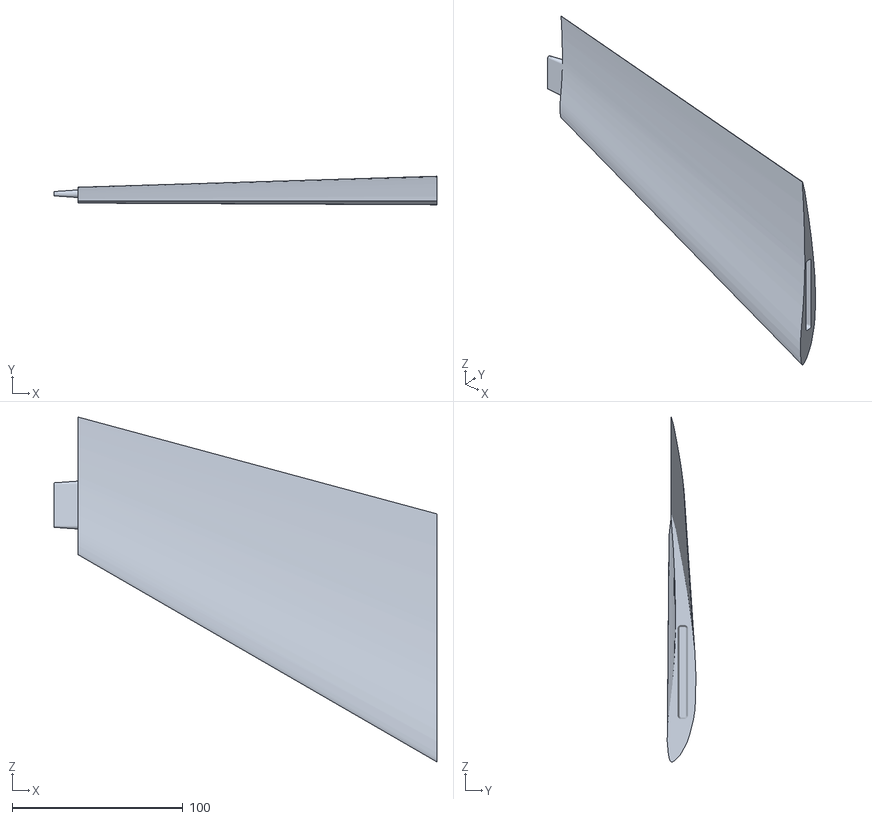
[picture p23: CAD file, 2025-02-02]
albatross_design/Wing tip right.STL
224.0 x 16.7 x 201.8

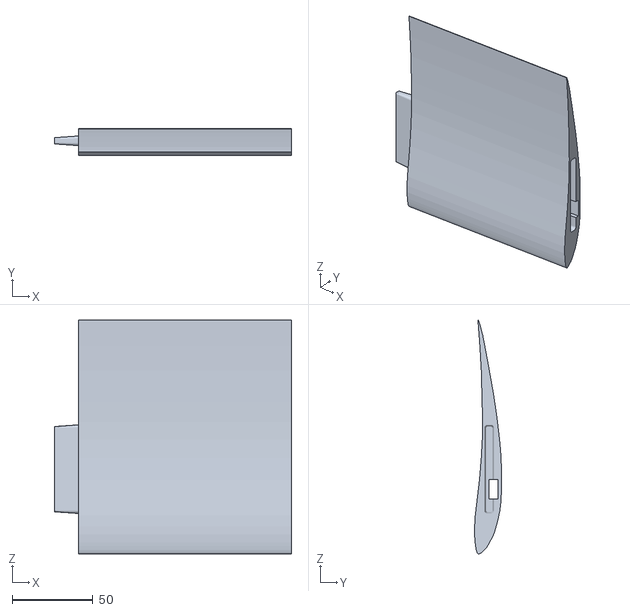
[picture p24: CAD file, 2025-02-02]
albatross_design/Wing middel plain - TODO times 2.STL
147.0 x 16.7 x 145.1

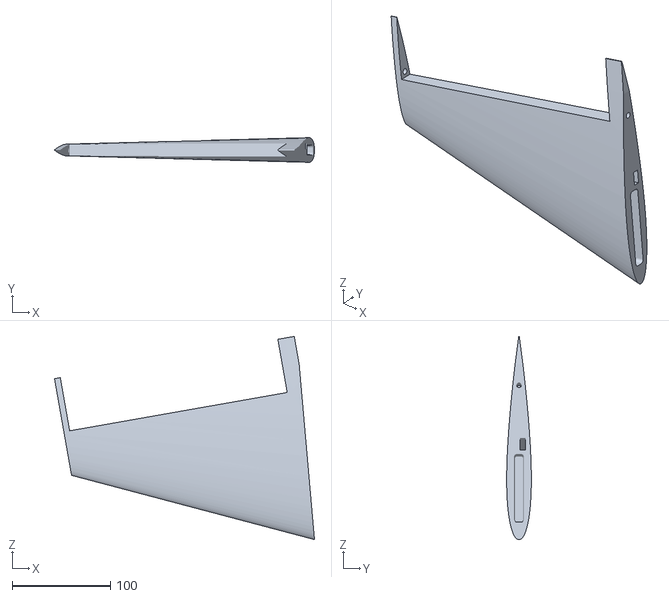
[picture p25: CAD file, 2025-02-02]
albatross_design/Horizontal stab mirror.STL
264.8 x 25.2 x 207.0

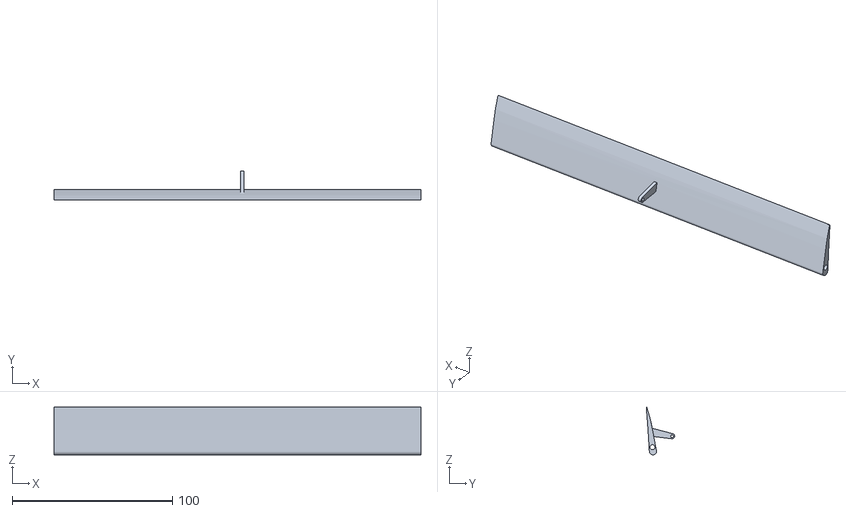
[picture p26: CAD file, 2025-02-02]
albatross_design/Flap - TODO2 times 2.STL
229.0 x 17.8 x 29.8

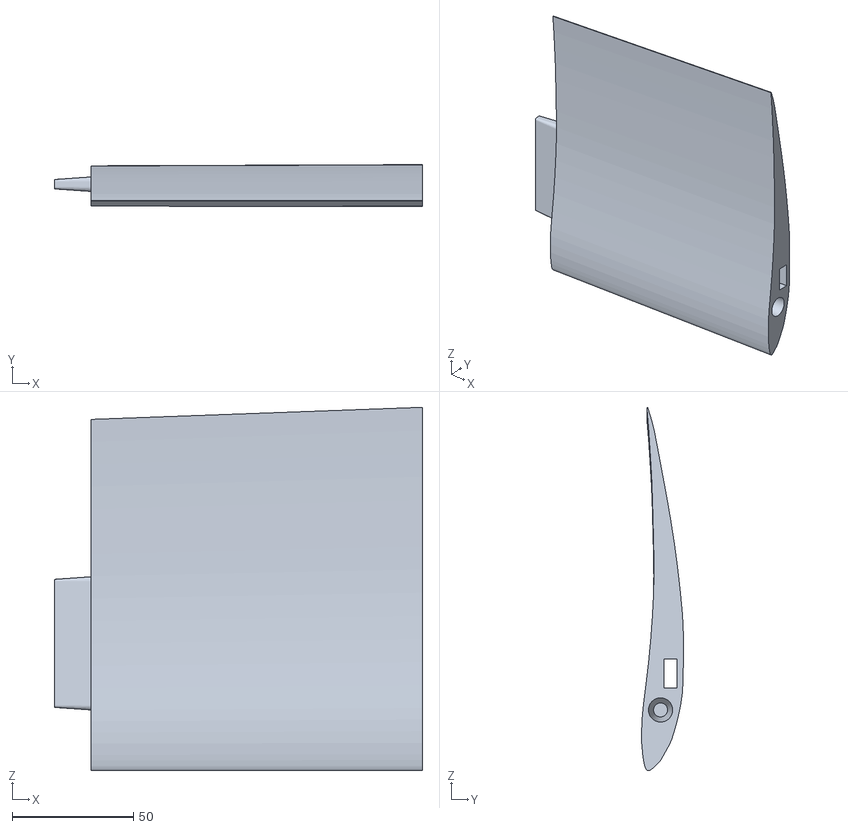
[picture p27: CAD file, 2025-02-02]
albatross_design/Wing L2 - TODO.STL
152.0 x 17.3 x 150.1

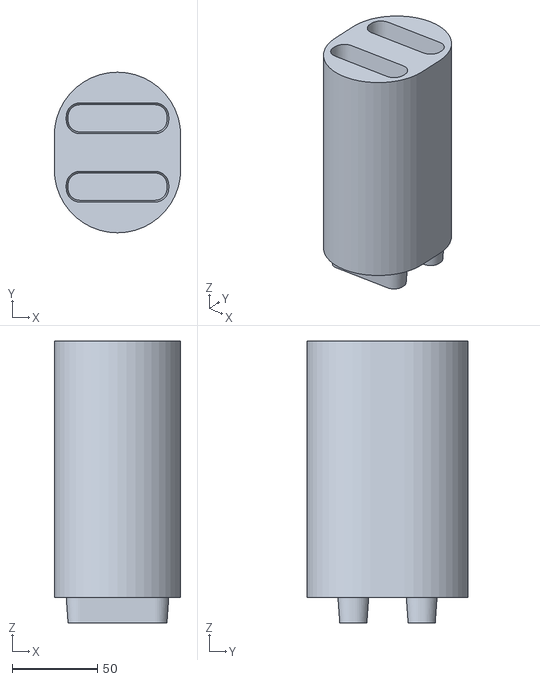
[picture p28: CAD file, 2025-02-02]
albatross_design/Extra body.STL
74.0 x 94.0 x 165.0

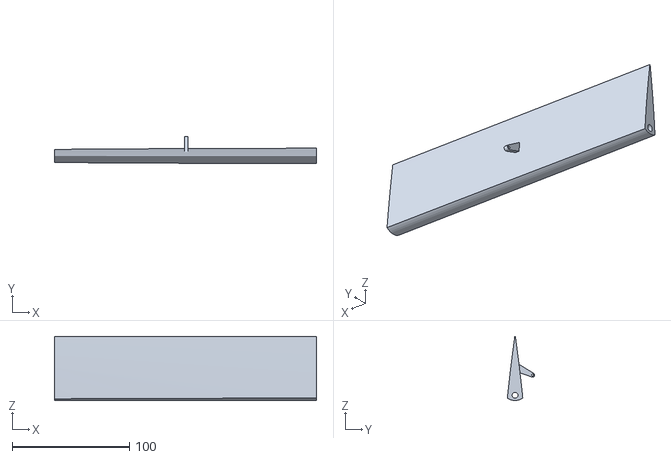
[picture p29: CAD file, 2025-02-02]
albatross_design/Flap hor. stab mirror.STL
223.0 x 23.3 x 54.5

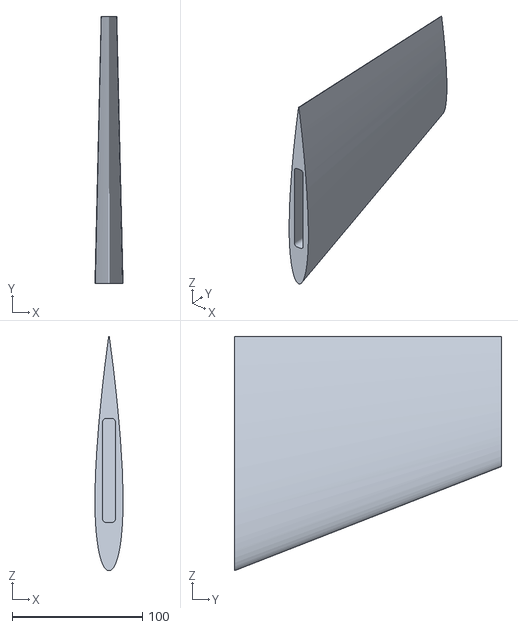
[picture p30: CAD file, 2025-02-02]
albatross_design/Vertical Stab.STL
21.6 x 205.0 x 180.0

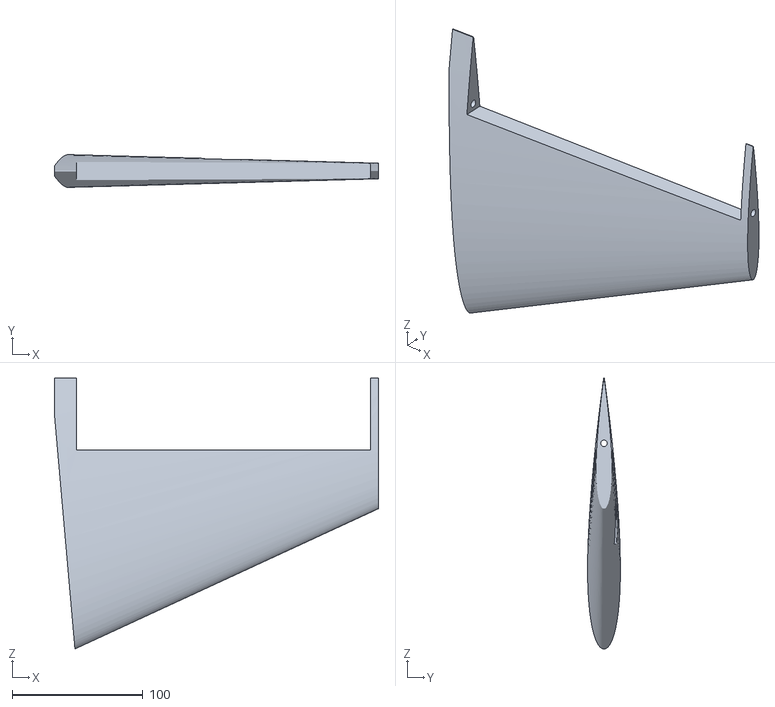
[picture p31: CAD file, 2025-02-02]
albatross_design/Horizontal stab.STL
248.0 x 25.2 x 207.4

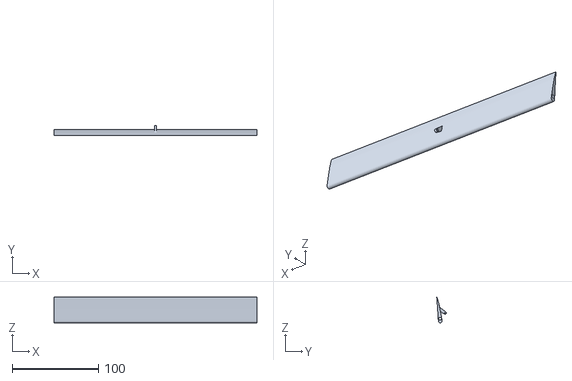
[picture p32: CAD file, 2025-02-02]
albatross_design/Flap.STL
235.0 x 11.2 x 29.8

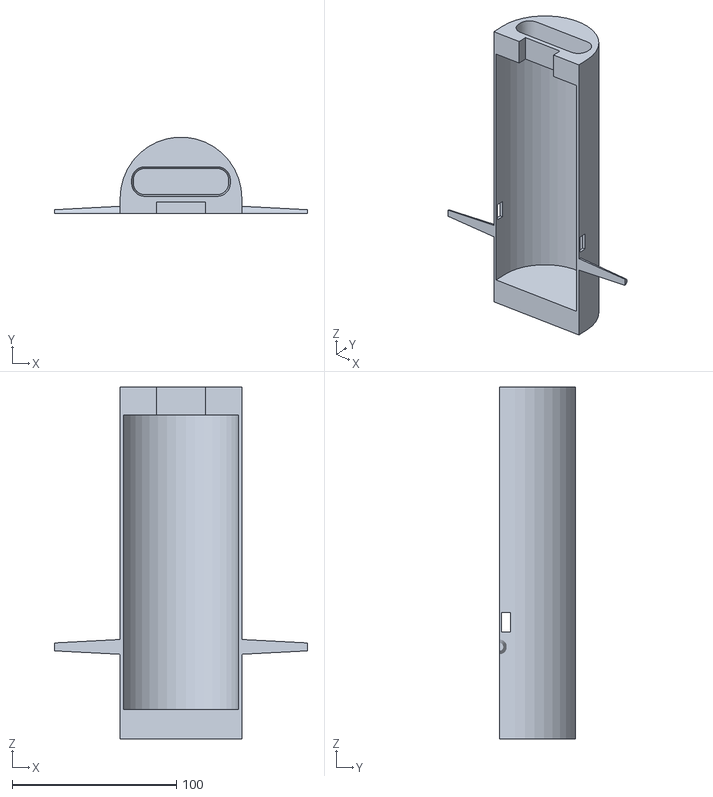
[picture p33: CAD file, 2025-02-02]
albatross_design/Cylinder body top - TODO1.STL
154.0 x 46.4 x 214.0

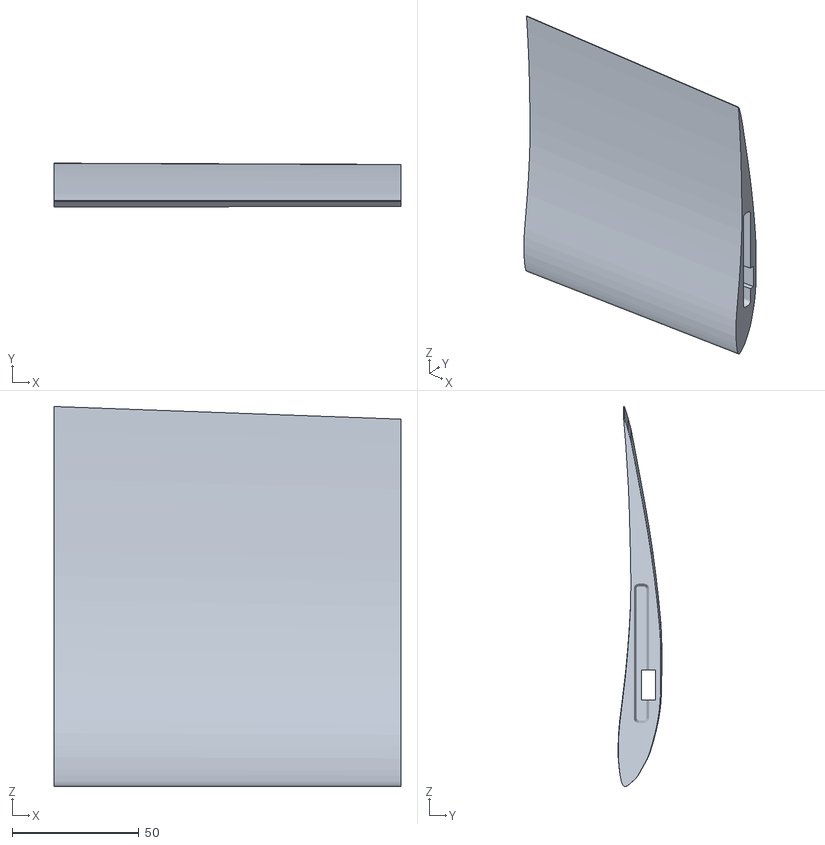
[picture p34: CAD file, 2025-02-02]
albatross_design/Wing L1 - TODO.STL
137.0 x 17.3 x 150.1

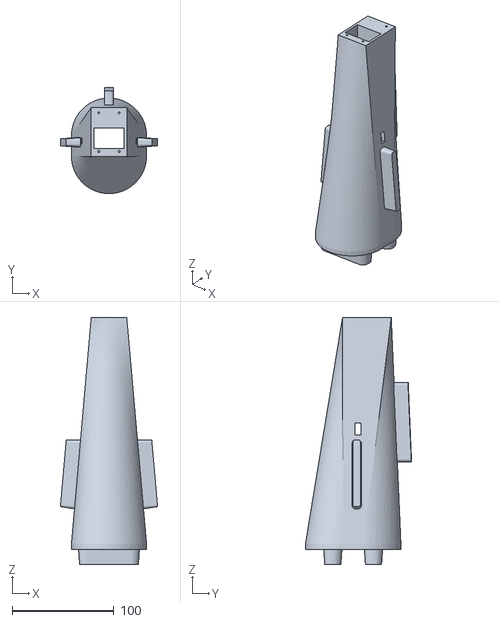
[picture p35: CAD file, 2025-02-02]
albatross_design/Tail.STL
95.6 x 104.5 x 243.0

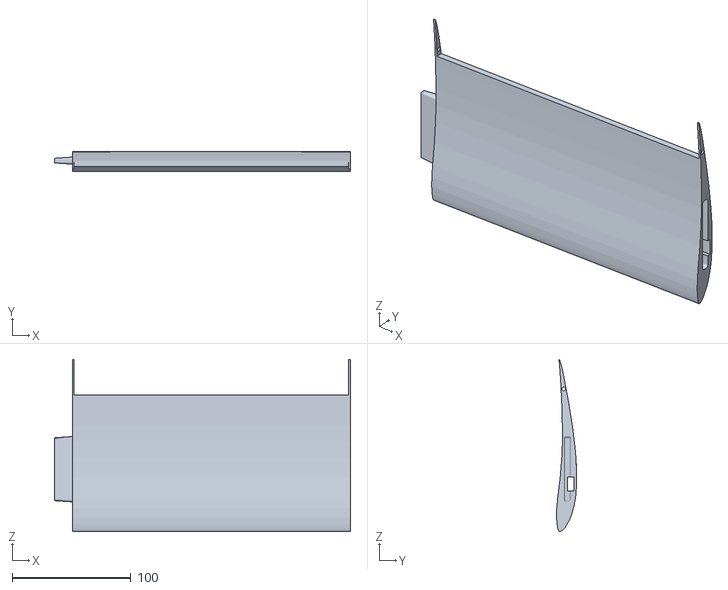
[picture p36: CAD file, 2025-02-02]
albatross_design/Wing flap - TODO2 times 2.STL
249.0 x 16.7 x 145.1

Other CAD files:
albatross_design/Wing tip left.STL
albatross_design/Extra body hole.STL
albatross_design/Flap hor. stab.STL
albatross_design/Cylinder body bottom - TODO1.STL
albatross_design/Nose plane.STL
albatross_design/Wing tip 1.1 v2 - TODO.STL

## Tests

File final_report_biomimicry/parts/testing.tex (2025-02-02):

\sectionauthor[Simon Blom; Sameh Mikhail]{Testing}
% The Testing section of your report is essential for demonstrating the effectiveness of your prototype under various conditions. This section is vital to prove not just that your design works, but how well it works, particularly in relation to the variable you've chosen to optimize. Your approach to testing should demonstrate a thorough, scientific method of evaluation, showcasing a deep understanding of your prototype's performance.
% \begin{itemize}
%     \item Testing Method: Clearly outline your testing methods, including the setup and conditions of the tests. Crucially, identify at least one key variable that you have chosen to optimize for in your design. This variable should be central to the performance and objectives of your prototype.
%     \item Results: Present the results of your tests in an organized and understandable manner. Utilize tables, graphs, and charts to effectively illustrate your findings, ensuring that they are directly related to the chosen variable for optimization and other tested parameters.
%     \item Analysis: Provide a critical analysis of your test results. Discuss the implications of the findings in relation to your project goals and the variable you aimed to optimize. Look for trends, patterns, or significant observations that emerge from the data and articulate what these mean for the effectiveness of your prototype.
% \end{itemize}

\subsection{Wind tunnel}
One of the important aspects that can be tested is the drag and lift in the air. It was tried to do a computational simulation on the wings and the plane, but due to unforeseen circumstances it was tackled in a different way. The Makerspace has a wind tunnel that was put to great use.

The wind tunnel setup allows for the precise measurement of aerodynamic forces acting on the wing. The fan generates a consistent airflow, simulating flight conditions, while the pressure sensors monitor the air pressure before and after the wing. This helps determine the pressure differential contributing to lift and drag.

The wing is mounted on a fixture designed to minimize interference with the airflow. The weight scales are calibrated to measure the forces in two directions: one aligned with the airflow (drag) and one perpendicular to it (lift). This configuration ensures accurate readings that reflect the wing's aerodynamic performance.

Before testing, a baseline measurement is taken with the wing absent to account for the drag induced by the apparatus itself. The wing is then mounted. Various angles of attack are tested to observe how the lift and drag vary with orientation. Data collected from the weight scales and pressure sensors are recorded and analyzed.

\begin{figure}[h]
    \centering
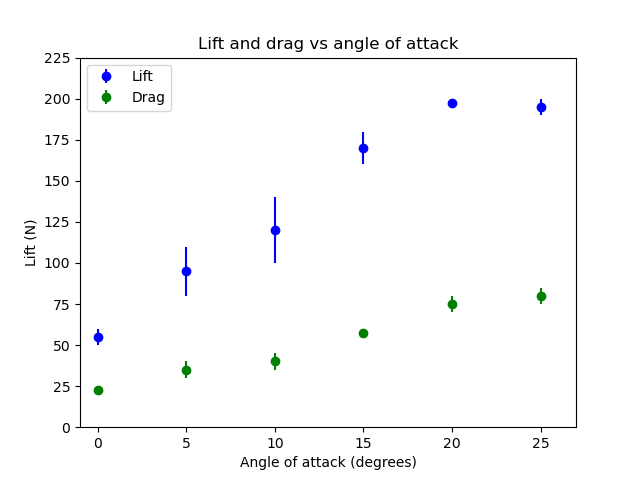
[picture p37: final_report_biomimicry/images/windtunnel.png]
    
    \caption{Measurements of the lift and drag varying the angle of attack}
\end{figure}

\noindent and to make these results more valid, a linear fit based on the equations of motion was applied 

\begin{figure}[h]
    \centering
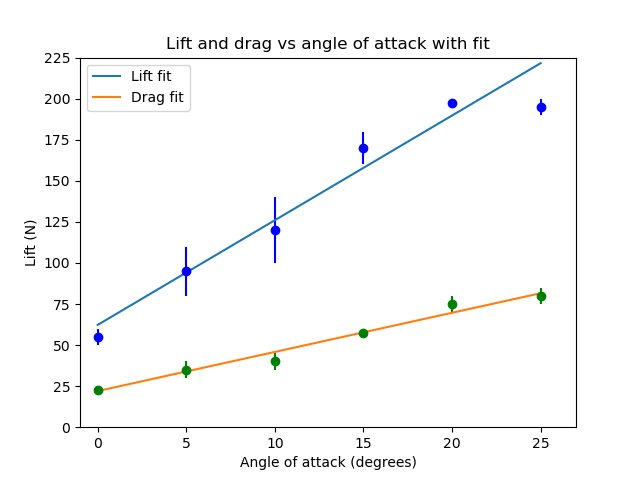
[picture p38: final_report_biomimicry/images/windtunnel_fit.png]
    
    \caption{Fit of the measurements of the lift and drag varying the angle of attack}
\end{figure}

\noindent resulting in the equations for the lift and drag

\begin{equation}
    L = 6x + 62 \qquad \text{and} \qquad D = 2.4x + 22
\end{equation}
with $L$ and $D$ the weight of the lift and drag in terms of grams and $x$ the angle of attack of the wind. This is not an `infinite' linear relation: after 25 degrees the wing vibrated and changed angle so that the results after that became invalid.

One of the best indications if the results are valid is the so called reduced chi-squared $\chi_{\nu}^{2}$. The results are valid if the chi-squared is around the one. The first equation (of the lift) has a reduced chi-squared of 10 and the second equation (of the drag) has a reduced chi-squared of 0.7. If the reduced chi-squared is above one, like in this case, the errors might be to small. This is visible in the data: the first and last two point are too small and the fit does not go through the point or the error. A reduced chi-squared of 0.7 is very good, so that equation is valid. An argument for the validity of both functions is that when the angle is zero, the value for the function corresponds to the meassured value.

\subsection{Motor and prop thrust}
When the electrical circuit was fully assembled and soldered together, a test setup was constructed with tools available at this time around the Makerspace, as visible in Figure \ref{fig:Motor testing setup}. The brushless motor, the Pichler Boost 10, was clamped to a vice with an APC E 6x4 propellor attached. Then, this contraption was attached to a scale using Duck-tape and set to zero.

This was simultaneously the first time a wireless connection between the Ground Control Station (Simon's laptop) and parts of the Albatrone was attained. After changing a lot of parameters in the software, the motor's RPM was able to be fully controlled by the throttle stick on the remote.

The testing contraption was mounted on a few degrees angle because of the limits on the vice, the measured values will have a small margin of error. With full throttle, 393 grams of thrust was measured, which was within the expected margins of the calculated values using \cite{RCPlanes}. 

"In order to get reasonable climb and acceleration capabilities, the Static Thrust should be at least about 1/3 of the planes' weight." \cite{RCPlanes}. The weight of electronics used, were in on around 400 grams. This leaves 800 grams for the filament. This goal is expected to be attainable. Even if this 1/3 Static Thrust goal is not met, the drone should still be able to achieve stable flight, but with the catch of less maneuverability.

\begin{figure}[h]
     \centering
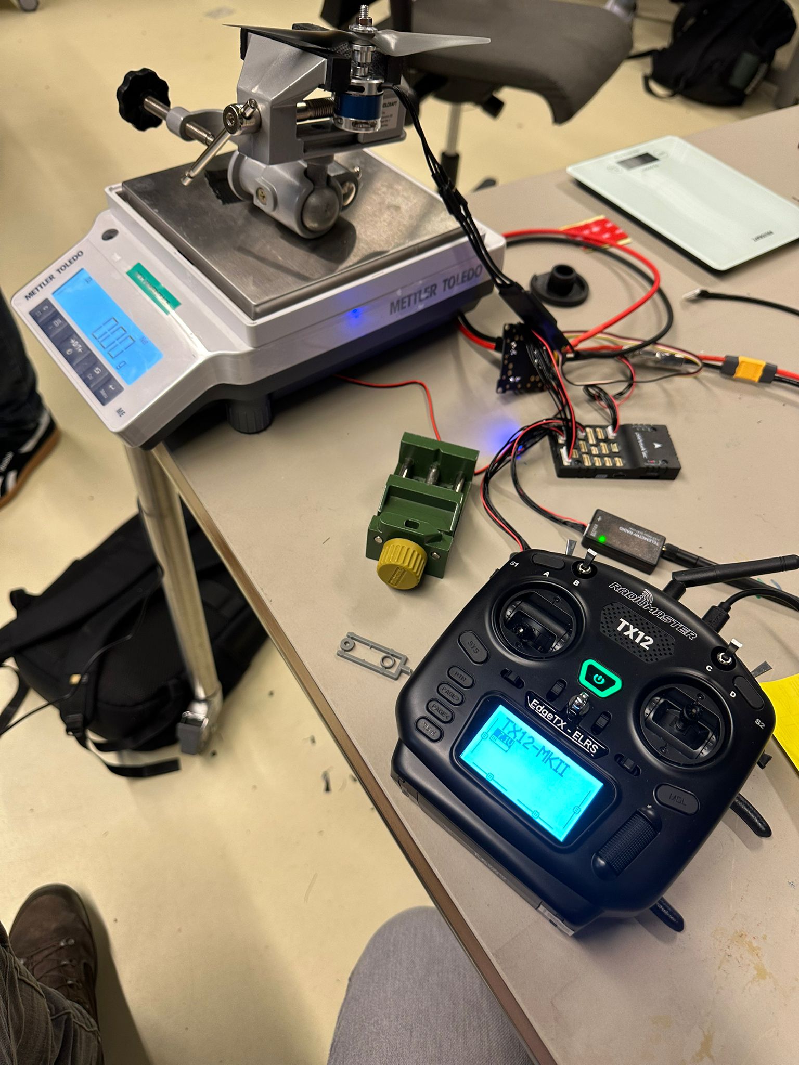
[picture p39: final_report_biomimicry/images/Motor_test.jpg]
     
     \caption{The motor testing setup}
     \label{fig:Motor testing setup}
 \end{figure}

\subsection{Connection range}
Since the goal is to construct something that is able to fly, it is important to know the range from which this prototype can be controlled. As of writing this report, the RC controls of the airplane is run through the telemetry link as there is no need to extended the range of a seperate RC link via ELRS \cite{ELRS} for this prototype. 

The Telemetry link consists of 2 100mW Holybro SiK Telemetry V3 Radios  of the 433MHz variant. One is plugged into the Ground Control Station, see Figure \ref{fig:range}, and the other is plugged into the Pixhawk 6C, the Flight Controller chosen for this prototype. This test was performed on the Science Park Campus, so the performance over the resulting range is expected to not be optimal due to signal interference. Full control of the attached servo and motor was attained, until around 200m, with stutters until 209m measured with GPS, see Figure \ref{fig:range}.

\begin{figure}
\centering
\begin{subfigure}{.5\textwidth}
  \centering
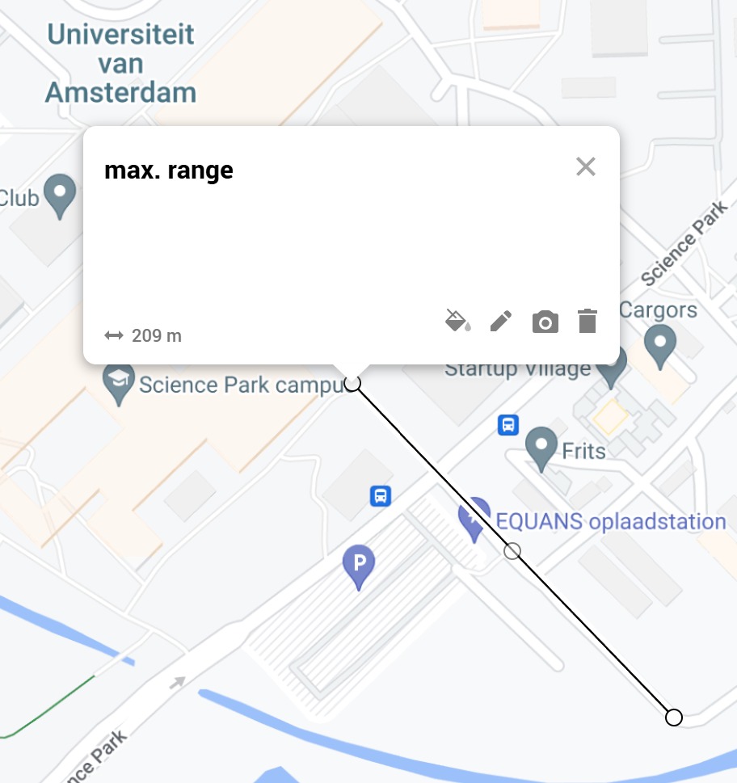
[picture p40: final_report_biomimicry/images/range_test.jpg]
  
  \label{fig:maxrange}
\end{subfigure}%
\begin{subfigure}{.5\textwidth}
  \centering
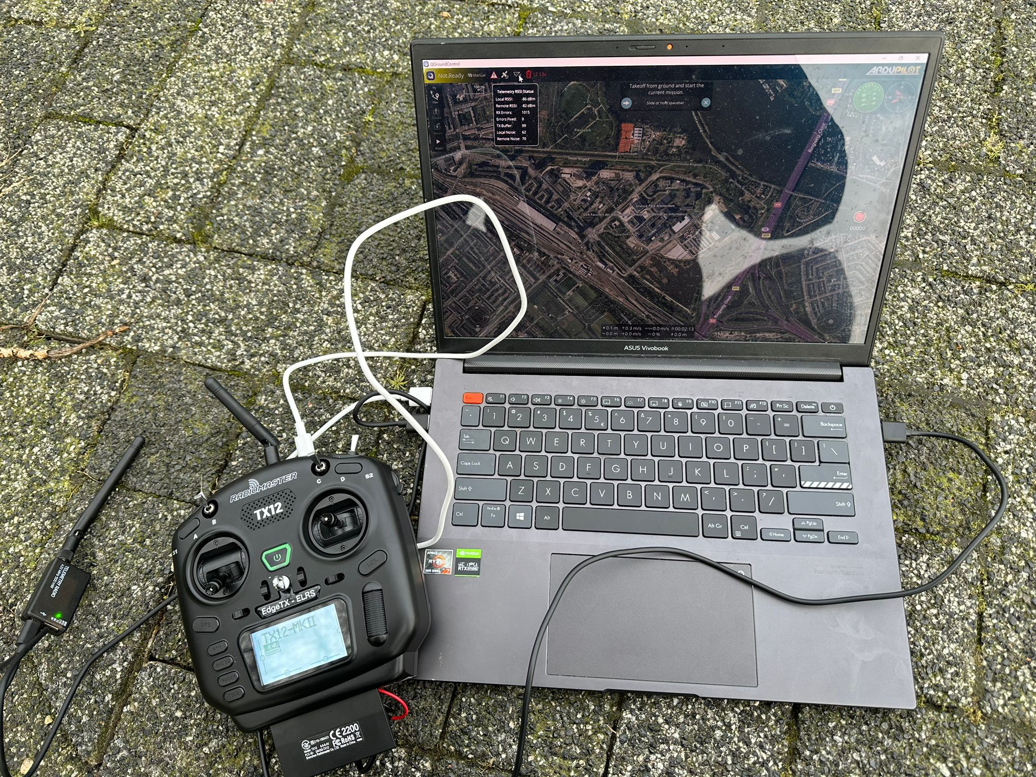
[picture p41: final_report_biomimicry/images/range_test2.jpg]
  
  \label{fig:rangesetup}
\end{subfigure}
\caption{The maximum range and testing setup}
\label{fig:range}
\end{figure}
